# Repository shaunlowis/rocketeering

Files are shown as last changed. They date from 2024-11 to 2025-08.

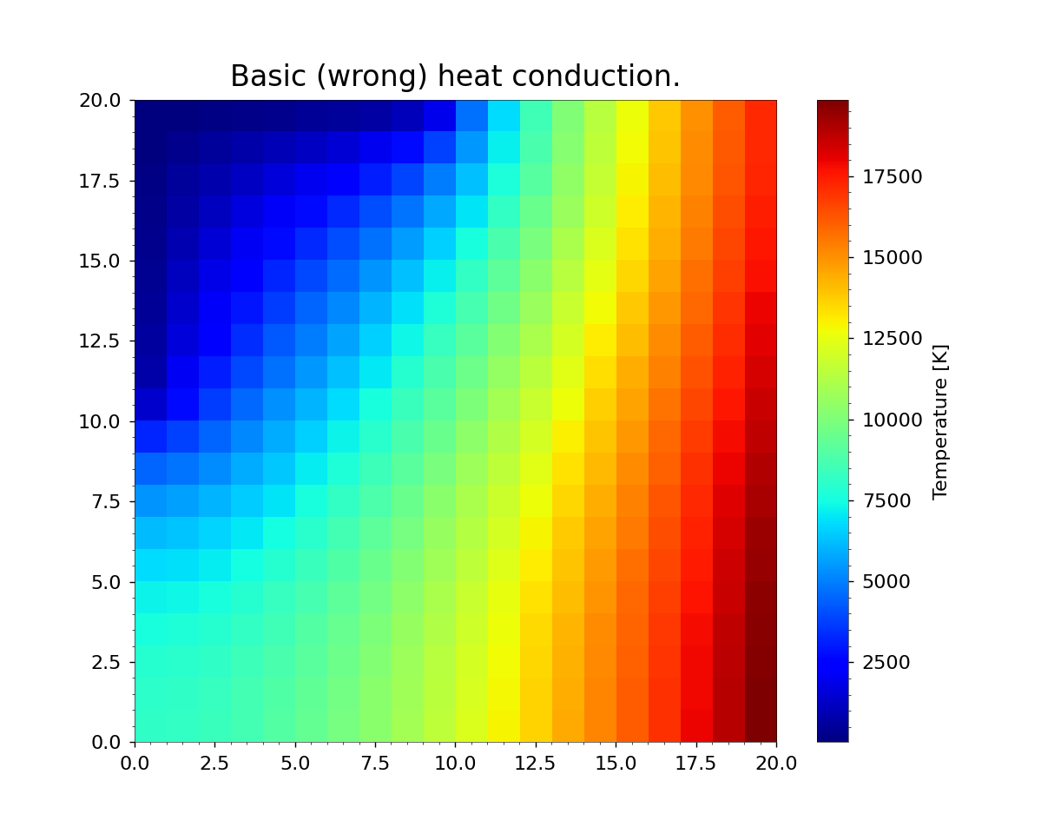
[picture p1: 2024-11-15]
modeling/thermal/babys_first_thermal.png

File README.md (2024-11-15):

# rocketeering
Documentation, progress and updates added [here](https://shaunlowis.github.io/rocketeering/)

NOTE: This guide, code, information and its authors assume no liability for outcomes or results of its use or distribution. All code and information is provided as-is for education purposes.

# Setup

Download appropriate version from [here](https://sourceforge.net/projects/sdcc/)

## Ubuntu

If on ubuntu, you should already have gcc and some form of python.

```
cd path-to-download

tar xjf sdcc-<some-version>.tar.bz

cd sdcc-<some-version>

# this will contain another file with the same name, move to that:
cd sdcc-<some-version>

# then run:
sudo ./configure

# you will probably have some missing dependencies, which I just installed with:
sudo apt install bison
sudo apt install flex
sudo apt install gputils

# repeat above until all requirements are met
# this will take quite a long time
make

# slightly faster
sudo make install

# if all went well:
sdcc -v

# which outputs something like:
SDCC : mcs51/z80/z180/r2k/r2ka/r3ka/sm83/tlcs90/ez80_z80/z80n/r800/ds390/pic16/pic14/TININative/ds400/hc08/s08/stm8/pdk13/pdk14/pdk15/mos6502/mos65c02 TD- 4.4.0 #14620 (Linux)
published under GNU General Public License (GPL)
```

Note; semi-useful guide on SDCC, see [here](https://martyn.welchs.me.uk/posts/installing-and-using-sdcc-on-linux/). For a more comprehensive guide, see the [user manual](https://sdcc.sourceforge.net/doc/sdccman.pdf).

Now we need to install the STM8 flash setup. I assume you have an ST-Link debugger, with a SWIM capable interface.
```
# wherever you want the repo to be
git clone https://github.com/vdudouyt/stm8flash.git

cd stm8flash

# dependencies:
sudo apt-get install pkg-config libusb-1.0-0-dev

make

sudo make install
```

### Download standard library
Source files for the STM8S Standard Peripheral Library are available from ST,
but it is more recommended to get the patched files from [here](https://github.com/roshbaby/stm8s-sdcc). Some further adjustments are required, depending on the
specific STM8 you have.

### Wiring the STLINK
We are using the STLINK-V2. The STM8 micro has to be debugged over SWIM.

Details for this are in section 7.3.3 [here](https://www.st.com/resource/en/user_manual/um2448-stlinkv3set-debuggerprogrammer-for-stm8-and-stm32-stmicroelectronics.pdf)

For debugging, connect SWO to the SWIM breakout header on the schematic and NRST TO NRST.

You may need to remove writing protection:

```
echo "00 00 ff 00 ff 00 ff 00 ff 00 ff" | xxd -r -p > factory_defaults.bin
stm8flash -c stlinkv2 -p stm8s007c8 -s opt -w factory_defaults.bin
```

## Flashing your first test program onto the STM8

In the `/flight_software` directory, simply do a `make flash` and if all goes well,
the compiled `main.c` file should be flashed onto your microcontroller.



Next up: make a makefile to first compile the stm8s_gpio.h and stm8s_gpio.c and 

## VS Code

Extensions:

- C/C++ for Visual Studio Code
- Hex Editor
- vscode-devdocs

## Possibly a much better setup:
https://github.com/bschwand/STM8-SPL-SDCC

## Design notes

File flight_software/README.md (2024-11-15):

# Debugger
Debug is available via [openocd](https://openocd.org/). Various windows install methods, I used [Chocolatey](https://community.chocolatey.org/packages/openocd). This installs it in `C:\ProgramData\chocolatey\lib`.

Openocd uses .cfg files to specify how to use boards (e.g. stm nucleo), targets (e.g. stm8s or even specific chips) and interfaces (e.g. stlink). These .cfg files are human readable and installed in the scripts folder of openocd, 
`C:\ProgramData\chocolatey\lib\openocd\tools\install\share\openocd\scripts`. See the [readme](https://openocd.org/doc-release/README) for more details.

`openocd -f interface/stlink-dap.cfg -f target/stm8s.cfg`

https://packages.msys2.org/package/mingw-w64-x86_64-gdb-multiarch?repo=mingw64
Needs mysys2 bin dir on path

# Coding notes/findings
## I2C is extremely tempermental. May appear to not work. Seems to randomly stop working with various history commits. Try:
 - Make clean
 - flash
 - unplug pwr, dbg, programmer
 - plug in pwr, dbg, programmer

## Printf Floats
Cannot printf floats by default, says `<NO FLOAT>`. See Compiler support routines of the [SDCC manual](docs/sdccman.pdf) for details. To enable add `-DUSE_FLOATS=1` to command line flags.
https://community.platformio.org/t/how-does-platformio-link-duse-floats-1/28458/14

## Alternate function remapping (Option byte programming)
To access the alternate pin functions you need to program the option byte accordingly. E.g. we use I2C on pins 16 & 17 which is their alternate function.

Option byte is in EEPROM and should be programmed a minimal number of times. You can use STVP as per [this guide](https://documentation.help/STM8-FlashTool-STVP/Prog0122.htm).

## Int type width only 2 bytes
On 32 bit systems ints are typically 4 bytes (STM32) and also in 64-bit AIX and Linux applications. In SDCC it is only 2 bytes (same as AVR actually) as per section 1.1 of the [SDCC manual](docs/sdccman.pdf). Therefore code such as `uint32_t comparison = 1<<(length - 1);` does not work as expected for length>16. This is because the 1 defaults to an int, and trying to leftshift it more than 16 bits is outside its width. You must specify the 1 as a 32 bit int, e.g. `uint32_t comparison = (uint32_t)1<<(length - 1);`

Lesson is to make code portable between different devices you shouldn't rely on the type widths being the same. And when taking code from forums/gpt, try specifying the compiler. Looking/Asking for C code is not enough.

## Interrupts
You need to match your interrupt handler function to the interrupt vector, so that your ISR actually gets called when the interrupt happens. This is achieved using the IRQ no assigned to the interrupt in the Interrupt Vector Mapping table of thhe STM8S007C8 Datasheet. 

E.g. UART3 RX full is number 20 with vector address 0x008058

## SD Card init/working
SD cards work based on [commands](https://chlazza.nfshost.com/sdcardinfo.html). Must send in certain order to init and expect correct responses. Demo [here](http://www.rjhcoding.com/avrc-sd-interface-3.php) but like [this guy](https://stackoverflow.com/questions/8080718/sdhc-microsd-card-and-spi-initialization) I had to also remove the CMD55 and set HCS bit in CMD1. Might be wrong.

https://github.com/joaquimorg/STM8SProjects/tree/master look in FM folder

SD card code only works when built on work laptop :)

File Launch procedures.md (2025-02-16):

# The day before
- Charge camera battery
- Charge flight comp battery
- Charge launch battery
- Clear camera SD
- Clear flight comp SD, NOT CONFIG.txt
- Pack as per below
- Charge laptops

# Packing list
- Laptops
- 5X filled 20L water containters (from work)
- 12V SLA car battery
- Rocket lower airframe
- Rocket upper airframe
- Nosecone
- Avionics bay with flight comp, flight comp battery, all fasteners
- Camera
- Camera lid
- Solid rocket motor box, containing
    - black powder
    - red plastic ejection charge cap
    - E-match
    - Motor baseplate
    - Baseplate nuts x2
    - Instructions
    - Washer for ejection charge
- Send it button with cable attached
- Flight comp debugging box with programming and debugging cables
- Spare flight comp battery
- Thermocouple
- Masking tape
- Toolbox with allen keys and screwdrivers
- Spare fasteners bag (inc spare motor washer)
- Spare ematch (red one angus)
- SD card reader
- Launch rail
- Fire extinguisher
- Water spray bottle (filled up)
- USB C charge + battery bank
- Camera lens cleaner (glasses cleaner?)

# The day of
- Ensure launch button is unplugged
- Check launch button is depressed (down = on, up = off)
- Begin recording camera
- Polisjh camera lens
- Connect battery to flight computer
- Check Green LED flashing at 20 Hz
- Check yellow LED on SD card writer is flashing
- Check RED LED not toggling
- Install AvBay
- Connect thermocouple to flight comp
- Install nosecone
- Follow motor instructions to install ejection charge
- Install motor, with backing plate
- Install E-Match as per rocket motor instructions
- Install thermocouple
- Mount to rail
- Everyone move to safe distance, from now assume rocket can launch at any point
- Connect ematch cable to battery
- Countdown
- Launch

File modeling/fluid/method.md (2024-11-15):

# OpenFOAM setup

Install from here:
https://develop.openfoam.com/Development/openfoam/-/wikis/precompiled/debian

I quickly did the basic tutorial case, but we want to use our own geometry, so let's follow:
https://www.cfd-online.com/Forums/openfoam-meshing/227156-setting-up-case-using-stl-files.html

Extended full tutorial on this is here:
https://wiki.openfoam.com/index.php?title=Tutorials

# Geometry

I whipped up the nose cone we will use for our rocket in onshape:
https://cad.onshape.com/documents/872890136eee2b11197cc0fd/w/8573091cfe1338d2f6237b9b/e/5a896293689c78557f90fb08

# Visualisation
I used ParaView. It is a little unintuitive, but you download it from here:
https://www.paraview.org/download/

Then you unzip/tar it, and you launch it with the `extracted_folder/bin/paraview` executable.

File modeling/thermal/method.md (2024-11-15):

# Heat conduction simulation to thermocouple
The thermocouple we use is intended to measure the motor's
exhaust stream. We use an RS PRO Type K, 1.5mm diameter which
has a 310 stainless steel sheath. This has a melting point of
around 1400C, which is below the expected motor temperature

## Python setup

```
# on ubuntu:
cd modeling/thermal
python3.10 -m venv .venv
source .venv/bin/activate 

python -m pip install -r requirements.txt
```

# Nose cone heating estimation
In the simplified case, estimate the expected heat of the nose
cone at different speeds. This is to inform at which mach regime
a new (metal) nose cone is required.

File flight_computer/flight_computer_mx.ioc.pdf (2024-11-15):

## flight_computer_mx Project Configuration Report

# 1. Description

## 1.1. Project

Project Name | flight_computer_mx
Board Name | No information
Generated with: | STM8CubeMX 1.5.0
Date | 06/23/2024

## 1.2. MCU

MCU Series | STM8S
MCU Line | STM8S Value Line
MCU name | STM8S007C8Tx
MCU Package | LQFP48
MCU Pin number | 48

# 2. Pinout Configuration

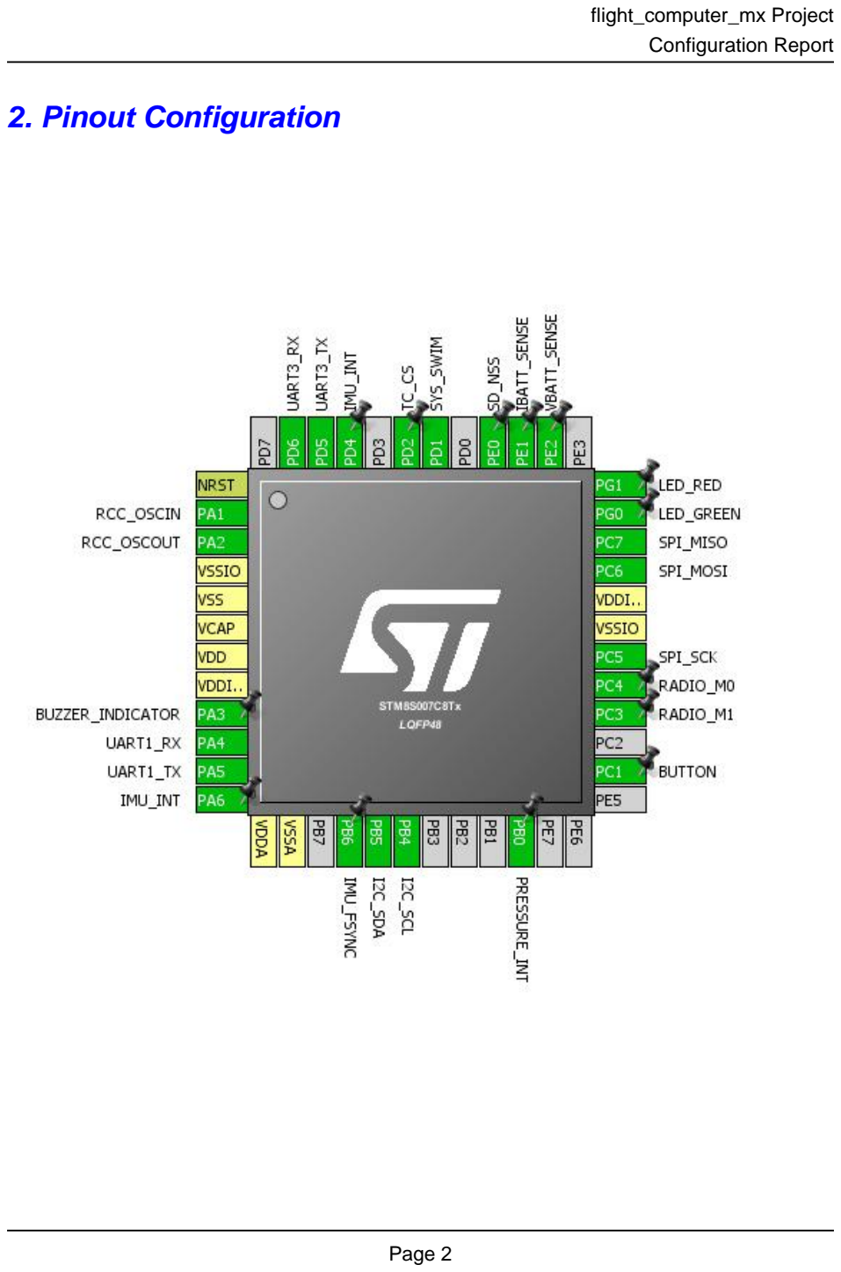
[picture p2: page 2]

# 3. Pins Configuration

Pin Number LQFP48 | Pin Name (function after reset) | Pin Type | Alternate Function(s) | Label
1 | NRST | Reset
2 | PA1 | I/O | RCC_OSCIN
3 | PA2 | I/O | RCC_OSCOUT
4 | VSSIO | Power
5 | VSS | Power
6 | VCAP | Power
7 | VDD | Power
8 | VDDIO | Power
9 | PA3 * | I/O | GPIO_Output | BUZZER_INDICATOR
10 | PA4 | I/O | UART1_RX
11 | PA5 | I/O | UART1_TX
12 | PA6 * | I/O | GPIO_Input | IMU_INT
13 | VDDA | Power
14 | VSSA | Power
16 | PB6 * | I/O | GPIO_Output | IMU_FSYNC
17 | PB5 | I/O | I2C_SDA
18 | PB4 | I/O | I2C_SCL
22 | PB0 * | I/O | GPIO_Input | PRESSURE_INT
26 | PC1 * | I/O | GPIO_Input | BUTTON
28 | PC3 * | I/O | GPIO_Output | RADIO_M1
29 | PC4 * | I/O | GPIO_Output | RADIO_M0
30 | PC5 | I/O | SPI_SCK
31 | VSSIO | Power
32 | VDDIO | Power
33 | PC6 | I/O | SPI_MOSI
34 | PC7 | I/O | SPI_MISO
35 | PG0 * | I/O | GPIO_Output | LED_GREEN
36 | PG1 * | I/O | GPIO_Output | LED_RED
38 | PE2 * | I/O | GPIO_Analog | VBATT_SENSE
39 | PE1 * | I/O | GPIO_Analog | IBATT_SENSE
40 | PE0 * | I/O | GPIO_Output | SD_NSS
42 | PD1 | I/O | SYS_SWIM
43 | PD2 * | I/O | GPIO_Output | TC_CS
45 | PD4 * | I/O | GPIO_Input | IMU_INT
46 | PD5 | I/O | UART3_TX
47 | PD6 | I/O | UART3_RX

## * The pin is affected with an I/O function

# 4. Clock Tree Configuration

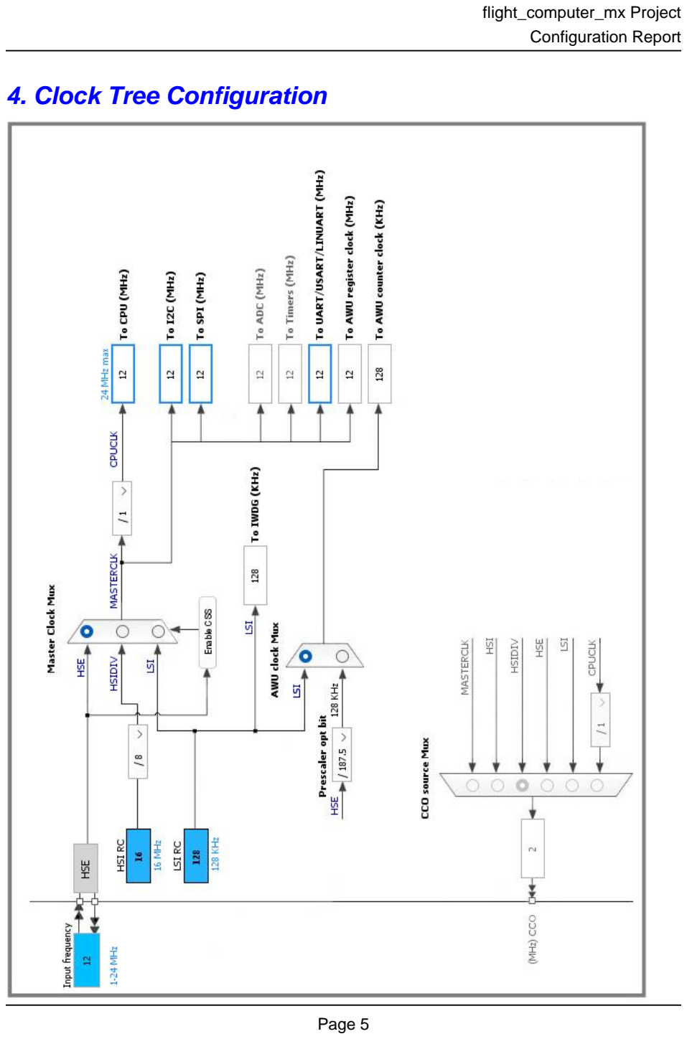
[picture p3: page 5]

# 5. Power Consumption Calculator report

## 5.1. Microcontroller Selection

Series | STM8S
Line | STM8S Value Line
MCU | STM8S007C8Tx
Datasheet | 22171_Rev5

## 5.2. Parameter Selection

Temperature | 25
Vdd | null

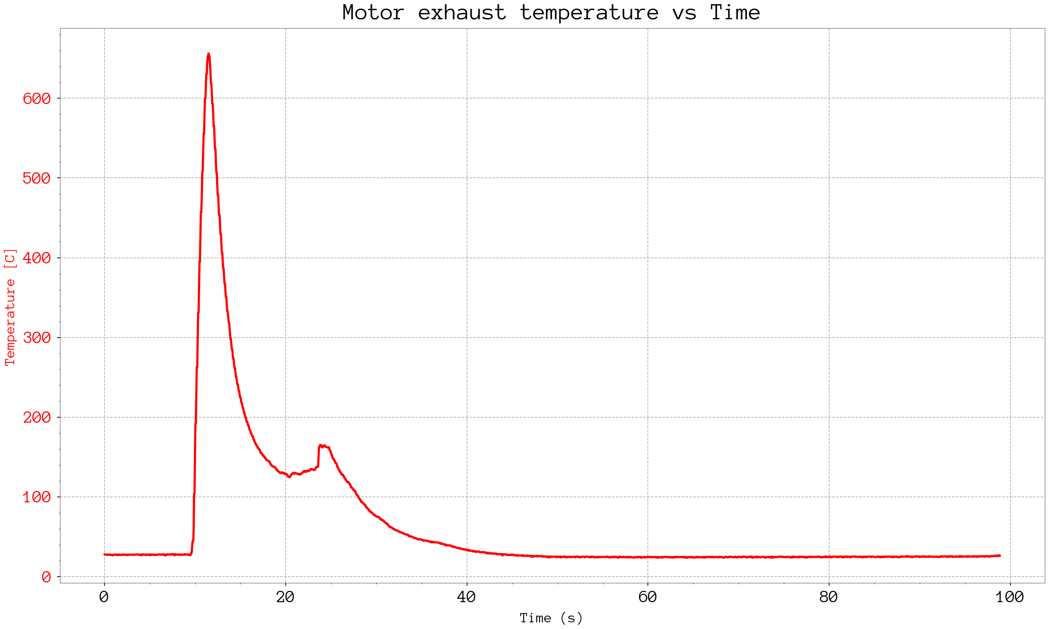
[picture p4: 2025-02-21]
thermocouple.png

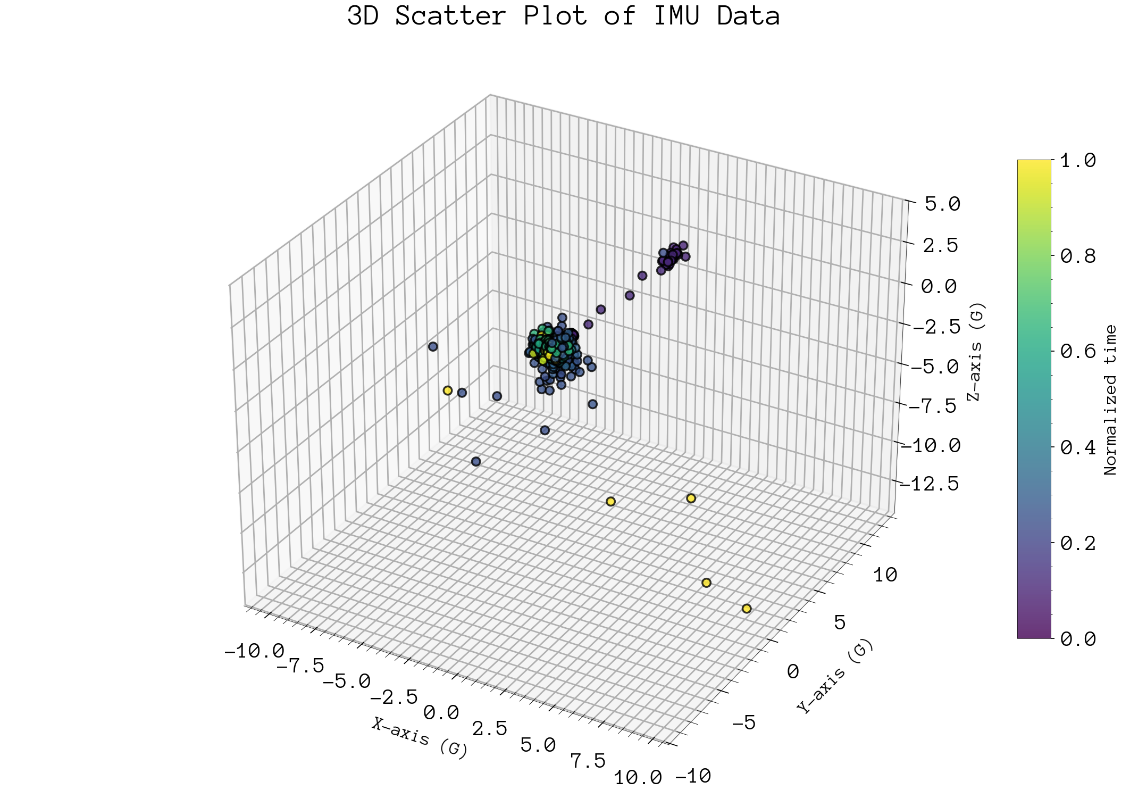
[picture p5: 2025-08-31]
imu_data.png

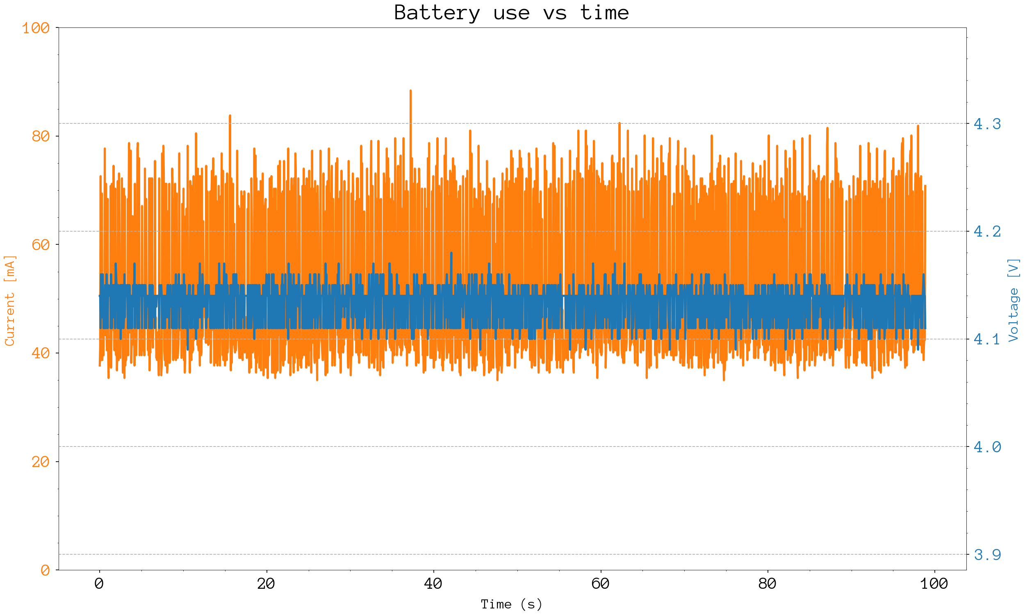
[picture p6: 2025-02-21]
battery.png

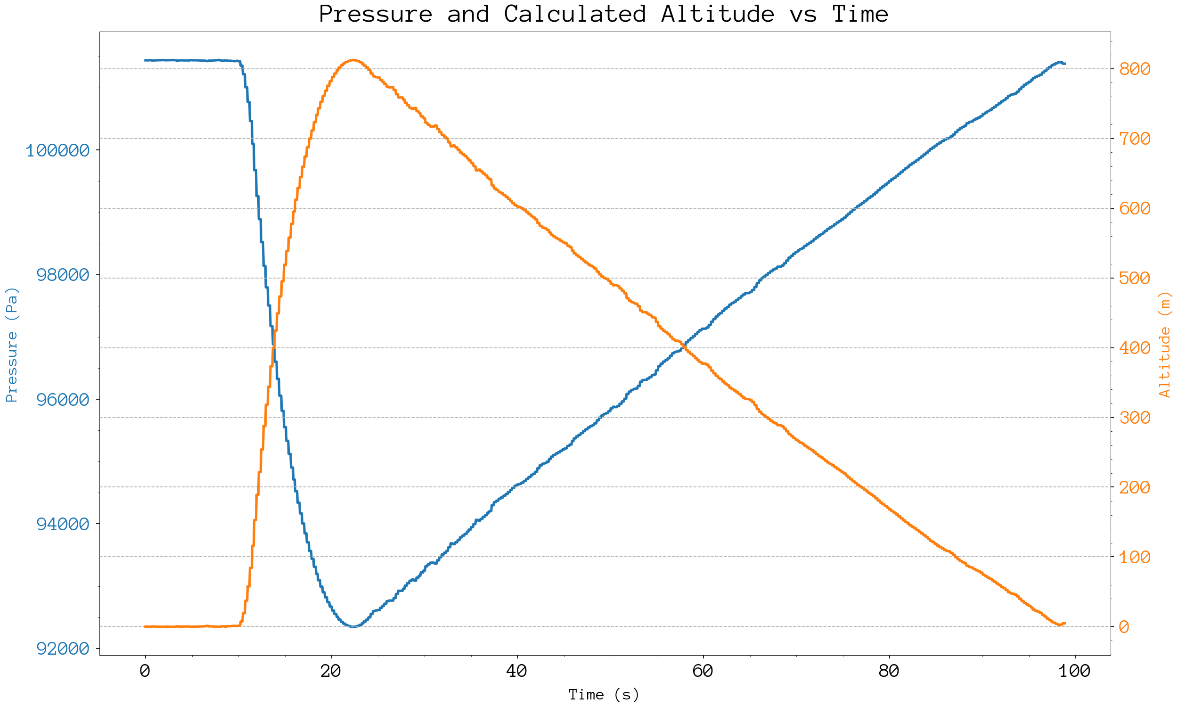
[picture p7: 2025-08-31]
altitude.png

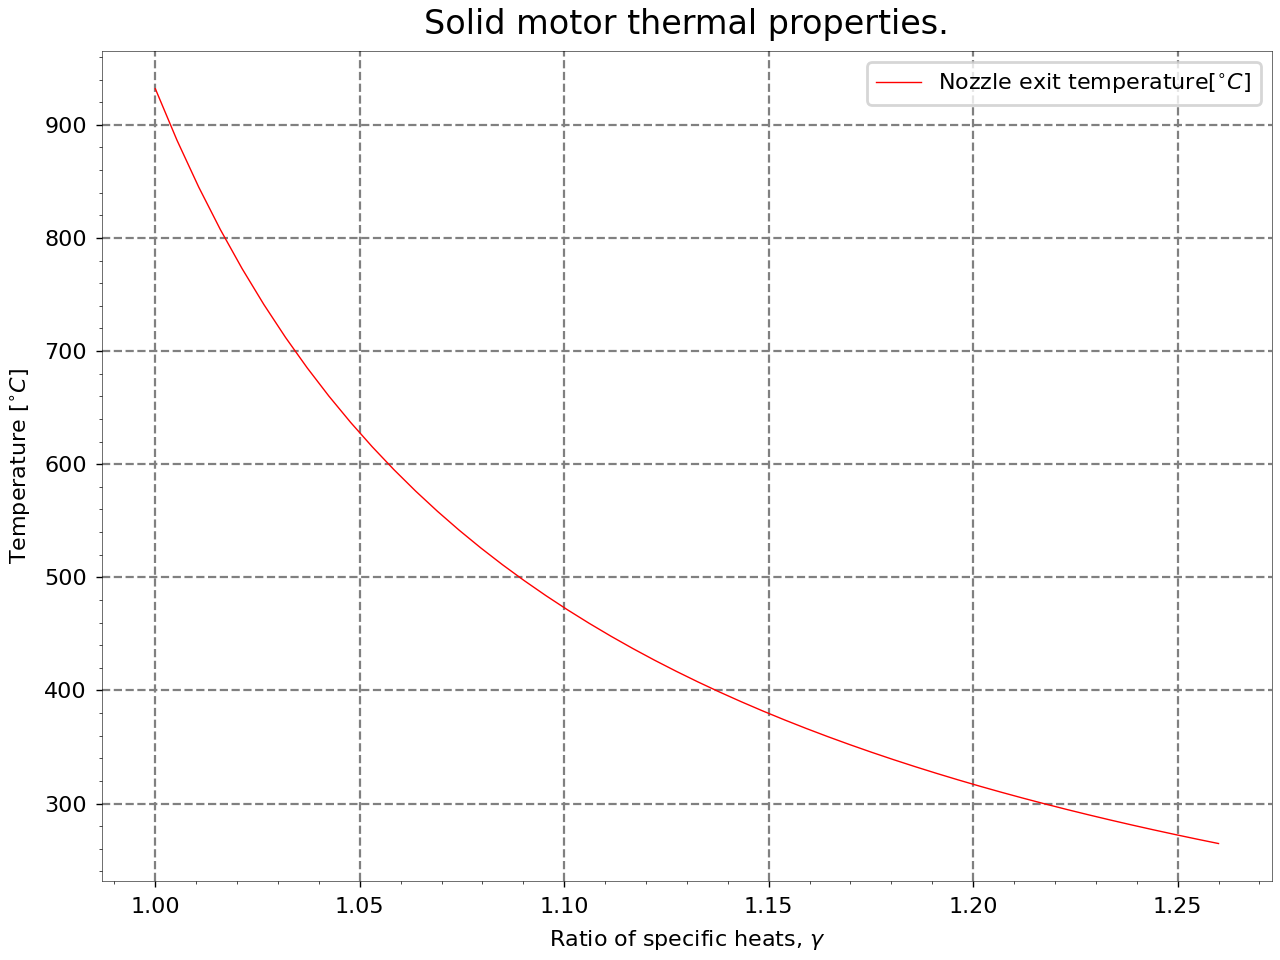
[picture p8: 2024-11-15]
modeling/thermal/nozzle_exit_temp.png

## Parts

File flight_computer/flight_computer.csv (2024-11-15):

Source: | C:\Users\angus\Documents\Electronics\Projects\rocketeering\flight_computer\flight_computer.kicad_sch
Date: | 30/05/2024 8:59:11 PM
Tool: | Eeschema 7.0.6
Generator: | C:\Program Files\KiCad\7.0\bin\scripting\plugins/bom_csv_grouped_by_value.py
Component Count: | 94
Collated Components:
Item | Qty | Reference(s) | Value | LibPart | Footprint | Datasheet | DNP | ESR | MPN | Manufacturer PN | Max Current | Power | Supplier | Supplier PN | Voltage
1 | 1 | BZ1 | Buzzer_indicator | Device:Buzzer | my_footprints:buzzer_Dia9.2mm_P5mm | https://www.digikey.co.nz/en/products/detail/soberton-inc/WST-0906T/16354832 |  |  |  | WST-0906T |  |  | Digikey | 433-WST-0906T-ND
2 | 8 | C1, C3, C10, C11, C17, C19, C20, C22 | 10uF | Device:C | Capacitor_SMD:C_0402_1005Metric | https://wmsc.lcsc.com/wmsc/upload/file/pdf/v2/lcsc/2304140030_Samsung-Electro-Mechanics-CL10A106KP8NNNC_C19702.pdf |  |  |  | CL10A106KP8NNNC |  |  | JLC | C19702 | 10V
3 | 16 | C2, C4, C8, C9, C12, C16, C18, C24, C25, C30, C33, C35, C36, C37, C38, C39 | 100nF | Device:C | Capacitor_SMD:C_0402_1005Metric | https://wmsc.lcsc.com/wmsc/upload/file/pdf/v2/lcsc/2304140030_Samsung-Electro-Mechanics-CL05B104KO5NNNC_C1525.pdf |  |  |  | CL05B104KO5NNNC |  |  | JLC | C1525 | 16V
4 | 2 | C5, C6 | 33pF | Device:C | Capacitor_SMD:C_0402_1005Metric | https://wmsc.lcsc.com/wmsc/upload/file/pdf/v2/lcsc/2304140030_FH--Guangdong-Fenghua-Advanced-Tech-0402CG330J500NT_C1562.pdf |  |  |  | 0402CG330J500NT |  |  | C1562 | JLC | 50V
5 | 4 | C7, C21, C23, C34 | 1uF | Device:C | Capacitor_SMD:C_0402_1005Metric | https://wmsc.lcsc.com/wmsc/upload/file/pdf/v2/lcsc/2304140030_Samsung-Electro-Mechanics-CL05A105KA5NQNC_C52923.pdf |  |  |  | CL05A105KA5NQNC |  |  | JLC | C52923 | 25V
6 | 2 | C13, C14 | 1.8nF | Device:C | Capacitor_SMD:C_0402_1005Metric | https://connect.kemet.com:7667/gateway/IntelliData-ComponentDocumentation/1.0/download/datasheet/C0402C182K3RACTU |  |  |  | 399-17371-1-ND |  |  | Digikey | C0402C182K3RAC7867
7 | 1 | C15 | 22pF | Device:C | Capacitor_SMD:C_0402_1005Metric | https://www.digikey.co.nz/en/products/detail/kemet/C0402C220K4RAC7867/8572389 |  |  |  | 399-17554-1-ND |  |  | Digikey | C0402C220K4RAC7867
8 | 2 | C26, C31 | 2.2uF | Device:C | Capacitor_SMD:C_0402_1005Metric | https://wmsc.lcsc.com/wmsc/upload/file/pdf/v2/lcsc/2304140030_Samsung-Electro-Mechanics-CL05A225MQ5NSNC_C12530.pdf |  |  |  | CL05A225MQ5NSNC |  |  | JLC | C12530 | 6.3V
9 | 2 | C27, C32 | 10nF | Device:C | Capacitor_SMD:C_0402_1005Metric | https://wmsc.lcsc.com/wmsc/upload/file/pdf/v2/lcsc/2304140030_Samsung-Electro-Mechanics-CL05B103KB5NNNC_C15195.pdf |  |  |  | CL05B103KB5NNNC |  |  | JLC | C15195 | 50V
10 | 2 | C28, C29 | 100pF | Device:C | Capacitor_SMD:C_0402_1005Metric | https://wmsc.lcsc.com/wmsc/upload/file/pdf/v2/lcsc/2304140030_FH--Guangdong-Fenghua-Advanced-Tech-0402CG101J500NT_C1546.pdf |  |  |  | 0402CG101J500NT |  |  | JLC | C1546 | 50V
11 | 1 | D1 | Green | Device:LED | LED_SMD:LED_0805_2012Metric | https://wmsc.lcsc.com/wmsc/upload/file/pdf/v2/lcsc/1806151820_Hubei-KENTO-Elec-KT-0805G_C2297.pdf |  |  |  | KT-0805G |  |  | JLC | C2297
12 | 1 | D2 | Red | Device:LED | LED_SMD:LED_0805_2012Metric | https://wmsc.lcsc.com/wmsc/upload/file/pdf/v2/lcsc/2304140030_Foshan-NationStar-Optoelectronics-NCD0805R1_C84256.pdf |  |  |  | NCD0805R1 |  |  | JLC | C84256
13 | 1 | D3 | 5.1V | Device:D_Zener | Package_TO_SOT_SMD:SOT-23 | https://www.mccsemi.com/pdf/Products/BZX84C(B)2V4~BZX84C(B)75(SOT-23).pdf |  |  |  | BZX84C5V1-TP |  |  | Digikey | BZX84C5V1-TPMSDKR-ND
14 | 1 | D4 | Blue | Device:LED | LED_SMD:LED_0603_1608Metric | https://wmsc.lcsc.com/wmsc/upload/file/pdf/v2/lcsc/2205171716_Everlight-Elec-19-217-BHC-ZL1M2RY-6T_C2986058.pdf |  |  |  | 19-217/BHC-ZL1M2RY/6T |  |  | JLC | C2986058
15 | 1 | F1 | 250mA | Device:Fuse | Fuse:Fuse_0603_1608Metric | http://www.kamaya.co.jp/upload/products_pdf/kamaya_products(FMC)_english_20170203_122640.pdf |  |  |  | FMC16501WBTP |  |  | Digikey | 2315-FMC16501WBTPDKR-ND
16 | 1 | J1 | Conn_02x05_Odd_Even | Connector_Generic:Conn_02x05_Odd_Even | Connector_PinHeader_2.54mm:PinHeader_2x05_P2.54mm_Vertical | ~ |  |  |  | 302-S101 |  |  | Digikey | ED1543-ND
17 | 1 | J2 | MEM2061-01-188-00-A_REVA | my_library:MEM2061-01-188-00-A_REVA | my_footprints:MEM2061-01-188-00-A | https://gct.co/files/specs/mem2061-spec.pdf |  |  |  | MEM2061-01-188-00-A |  |  | Digikey | 2073-MEM2061-01-188-00-ACT-ND
18 | 1 | J3 | Conn_01x02 | Connector_Generic:Conn_01x02 | Connector_JST:JST_PH_S2B-PH-K_1x02_P2.00mm_Horizontal | https://www.jst-mfg.com/product/pdf/eng/ePH.pdf |  |  |  | S2B-PH-K-S |  |  | Digikey | 455-1719-ND
19 | 1 | J7 | Conn_01x07_MountingPin | Connector_Generic_MountingPin:Conn_01x07_MountingPin | my_footprints:E220-400T30D | ~ |  |  |  | E220-400T30D
20 | 1 | L1 | 1.5uH | Device:L | Inductor_SMD:L_1008_2520Metric | https://search.murata.co.jp/Ceramy/image/img/P02/JELF243B-0019.pdf |  | 88mOhm |  | LQM2HPN1R5MG0L | 1.5A |  | Digikey | 490-5113-1-ND
21 | 1 | L2 | 3.3uH | Device:L | Inductor_SMD:L_0805_2012Metric | https://product.tdk.com/en/system/files |  |  |  | MLZ2012N3R3LT000 | 750mA |  | Digikey | 445-6759-1-ND
22 | 1 | Q1 | Q_NPN_BEC | Device:Q_NPN_BEC | Package_TO_SOT_SMD:SOT-23-3 | https://www.onsemi.com/download/data-sheet/pdf/bc846alt1-d.pdf |  |  |  | BC847CLT3G |  |  | Digikey | BC847CLT3GOSCT-ND
23 | 1 | Q2 | Q_NMOS_GSD | Device:Q_NMOS_GSD | Package_TO_SOT_SMD:SOT-323_SC-70 | https://www.panjit.com.tw/upload/datasheet/PJC7404.pdf |  |  |  | PJC7404_R1_00001 |  |  | Digikey | 3757-PJC7404_R1_00001CT-ND
24 | 5 | R1, R18, R22, R24, R25 | 150R | Device:R | Resistor_SMD:R_0402_1005Metric | https://wmsc.lcsc.com/wmsc/upload/file/pdf/v2/lcsc/2205311900_UNI-ROYAL-Uniroyal-Elec-0402WGF1500TCE_C25082.pdf |  |  |  | 0402WGF1500TCE |  |  | JLC | C25082
25 | 1 | R2 | 470R | Device:R | Resistor_SMD:R_0402_1005Metric | https://wmsc.lcsc.com/wmsc/upload/file/pdf/v2/lcsc/2205311900_UNI-ROYAL-Uniroyal-Elec-0402WGF4700TCE_C25117.pdf |  |  |  | 0402WGF4700TCE |  |  | JLC | C25117
26 | 7 | R3, R6, R14, R15, R16, R21, R23 | 1M | Device:R | Resistor_SMD:R_0402_1005Metric | https://wmsc.lcsc.com/wmsc/upload/file/pdf/v2/lcsc/2206010030_UNI-ROYAL-Uniroyal-Elec-0402WGF1004TCE_C26083.pdf |  |  |  | 0402WGF1004TCE |  |  | JLC | C26083
27 | 2 | R4, R5 | 4.7k | Device:R | Resistor_SMD:R_0402_1005Metric | https://wmsc.lcsc.com/wmsc/upload/file/pdf/v2/lcsc/2206010045_UNI-ROYAL-Uniroyal-Elec-0402WGF4701TCE_C25900.pdf |  |  |  | 0402WGF4701TCE |  |  | JLC | C25900
28 | 3 | R7, R10, R11 | 1k | Device:R | Resistor_SMD:R_0402_1005Metric | https://wmsc.lcsc.com/wmsc/upload/file/pdf/v2/lcsc/2206010216_UNI-ROYAL-Uniroyal-Elec-0402WGF1001TCE_C11702.pdf |  |  |  | 0402WGF1001TCE |  |  | JLC | C11702
29 | 3 | R8, R19, R20 | 0R | Device:R | Resistor_SMD:R_0402_1005Metric | https://wmsc.lcsc.com/wmsc/upload/file/pdf/v2/lcsc/2206010216_UNI-ROYAL-Uniroyal-Elec-0402WGF0000TCE_C17168.pdf |  |  |  | 0402WGF0000TCE |  |  | JLC | C17168
30 | 1 | R9 | 0.1R | Device:R | Resistor_SMD:R_1206_3216Metric | https://wmsc.lcsc.com/wmsc/upload/file/pdf/v2/lcsc/2205311900_UNI-ROYAL-Uniroyal-Elec-1206W4F100LT5E_C25334.pdf |  |  |  | 1206W4F100LT5E |  | 250mW | JLC | C25334
31 | 6 | R12, R26, R27, R28, R29, R30 | 10k | Device:R | Resistor_SMD:R_0402_1005Metric | https://wmsc.lcsc.com/wmsc/upload/file/pdf/v2/lcsc/2206010100_UNI-ROYAL-Uniroyal-Elec-0402WGF1002TCE_C25744.pdf |  |  |  | 0402WGF1002TCE |  |  | JLC | C25744
32 | 1 | R13 | 68k | Device:R | Resistor_SMD:R_0402_1005Metric | https://wmsc.lcsc.com/wmsc/upload/file/pdf/v2/lcsc/2206010030_UNI-ROYAL-Uniroyal-Elec-0402WGF6802TCE_C36871.pdf |  |  |  | 0402WGF6802TCE |  |  | JLC | C36871
33 | 2 | SW1, SW2 | SW_Push | Switch:SW_Push | my_footprints:KMR2_1 | https://www.ckswitches.com/media/1479/kmr2.pdf |  |  |  | KMR231GLFS |  |  | Digikey | 401-1429-1-ND
34 | 1 | U1 | STM8S007C8T6TR | my_library:STM8S007C8T6 | Package_QFP:LQFP-48_7x7mm_P0.5mm | https://www.st.com/content/ccc/resource/technical/document/datasheet/03/af/ba/15/7c/fe/4c/91/DM00037365.pdf/files/DM00037365.pdf/jcr:content/translations/en.D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 |  |  |  | STM8S007C8T6TR |  |  | Digikey | 497-18848-1-ND
35 | 1 | U2 | NCS325 | Amplifier_Operational:NCS325 | Package_TO_SOT_SMD:SOT-23-5 | http://www.onsemi.com/pub/Collateral/NCS325-D.PDF |  |  |  | NCS325SN2T1G |  |  | Digikey | NCS325SN2T1GOSCT-ND
36 | 1 | U3 | TPS63051RMWR | my_library:TPS63051RMWR | my_footprints:VQFN-12-HR_2.5x2.5mm_P0.5mm | https://www.ti.com/lit/ds/symlink/tps63051.pdf?ts=1714117211770 |  |  | TPS63051RMWR | TPS63051RMWR |  |  | Digikey | 296-42650-1-ND
37 | 1 | U4 | MIC94310-GYMT-TR | my_library:MIC94310-GYMT-TR | my_footprints:TDFN-4-1EP_1.2x1.6mm_P0.5mm | http://ww1.microchip.com/downloads/en/devicedoc/mic94310.pdf |  |  |  | MIC94310-GYMT-TR |  |  | Digikey | 576-4012-1-ND
38 | 1 | U5 | SPL07-003 | my_library:SPL07-003 | Package_LGA:ST_HLGA-10_2x2mm_P0.5mm_LayoutBorder3x2y | https://mm.digikey.com/Volume0/opasdata/d220001/medias/docus/4843/SPL07-003.pdf |  |  |  | SPL07-003 |  |  | Digikey | 4719-SPL07-003CT-ND
39 | 1 | U6 | YIC31612EBGG | my_library:YIC31612EBGG | my_footprints:24-SMD Module | https://www.yic.com.tw/wp-content/uploads/2022/01/YIC31612EBGG.pdf |  |  |  | YIC31612EBGG |  |  | Digikey | 3155-YIC31612EBGGCT-ND
40 | 1 | U7 | ICM-42670-P | my_library:ICM-42670-P | Package_LGA:LGA-14_3x2.5mm_P0.5mm_LayoutBorder3x4y | https://product.tdk.com/system/files/dam/doc/product/sensor/mortion-inertial/imu/data_sheet/ds-000451-icm-42670-p.pdf |  |  |  | ICM-42670-P |  |  | Digikey | 1428-ICM-42670-PCT-ND
41 | 1 | U8 | MAX31855KASA | Sensor_Temperature:MAX31855KASA | Package_SO:SOIC-8_3.9x4.9mm_P1.27mm | http://datasheets.maximintegrated.com/en/ds/MAX31855.pdf |  |  |  | MAX31855KASA+T |  |  | Digikey | MAX31855KASA+TCT-ND
42 | 1 | U9 | Antenna_GPS | my_library:1582AT54A0045 | my_footprints:1582AT54A0045 | https://www.johansontechnology.com/datasheets/1582AT54A0045/1582AT54A0045.pdf |  |  |  | 1582AT54A0045 |  |  | Digikey | 712-1582AT54A0045001ECT-ND
43 | 1 | Y1 | 12MHz | Device:Crystal_GND24 | Crystal:Crystal_SMD_3225-4Pin_3.2x2.5mm | https://wmsc.lcsc.com/wmsc/upload/file/pdf/v2/lcsc/2403291504_YXC-X322512MSB4SI_C9002.pdf |  |  |  | X322512MSB4SI |  |  | JLC | C9002

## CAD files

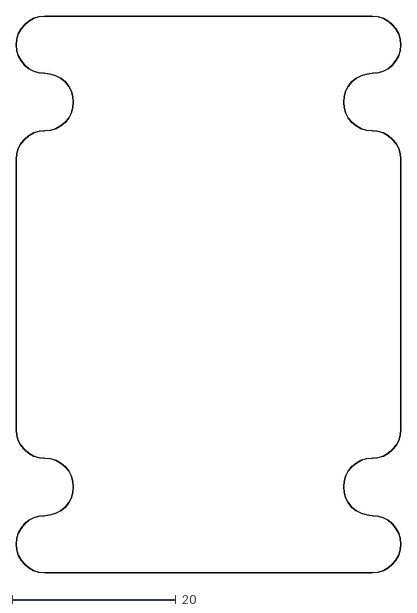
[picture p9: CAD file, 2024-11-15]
flight_computer/Flight computer outline.dxf
47.0 x 68.0

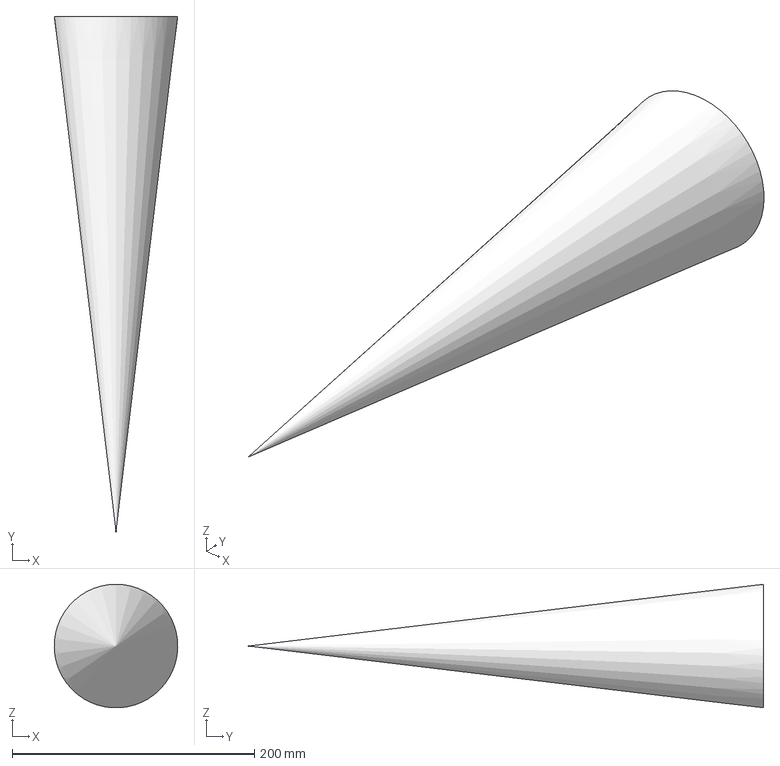
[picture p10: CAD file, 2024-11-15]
modeling/fluid/meshing/Nose cone.step
102.0 x 425.0 x 101.9 mm

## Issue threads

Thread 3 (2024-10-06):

Battery V/I sensing to wrong pins

AngusEason, 2024-10-06:
Not routed to analog pins

shaunlowis, 2024-10-11:
Fixed with rework wire

Closed 2024-10-11.

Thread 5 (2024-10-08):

Button footprints are wrong

AngusEason, 2024-10-08:

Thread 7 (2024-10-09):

Complete thermocouple setup

shaunlowis, 2024-10-09:
With current micro

shaunlowis, 2024-10-12:
got SPI init and raw reads done, need to do conversion and validation.

shaunlowis, 2024-11-01:
Adding datasheet to here for convenience:
https://www.analog.com/media/en/technical-documentation/data-sheets/max31855.pdf

shaunlowis, 2024-11-10:
Closed with latest FC_dev merge

Closed 2024-11-10.

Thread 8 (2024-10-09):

Visualise collected data

shaunlowis, 2024-10-09:
Doing a Rust backend and javascript frontend could be quite cool, here's what ChatGPT had to say:

Integrating Rust with a web interface for live plotting is a great way to make your data visualization accessible and interactive. You can achieve this by using Rust for the backend, serving the live data, and a JavaScript library like **Plotly.js** or **Chart.js** for rendering the live plots in a web browser.

Here’s a guide on how to do this with Rust using the **Rocket** web framework (for the backend) and **Plotly.js** (for the frontend).

### 1. **Setup Rocket Web Framework**

First, you'll need to install **Rocket**, a fast and flexible web framework for Rust.

#### In `Cargo.toml`:
Add the dependencies for `Rocket` and `Serde` (for serialization) in your `Cargo.toml`:

```toml
[dependencies]
rocket = { version = "0.5.0-rc.2", features = ["json"] }
serde = { version = "1.0", features = ["derive"] }
serde_json = "1.0"
tokio = { version = "1", features = ["full"] }
```

### 2. **Backend: Serving Live Data**

We’ll create a simple REST API endpoint that streams live data to the frontend. In a real-world scenario, this data would come from the radio link, but we’ll simulate it here.

#### `src/main.rs`:

```rust
#[macro_use] extern crate rocket;

use rocket::serde::{Serialize, json::Json};
use std::{thread, time::Duration};

// Simulated data point
#[derive(Serialize)]
struct DataPoint {
    x: u32,
    y: u32,
}

// API route that simulates live data
#[get("/live_data")]
fn live_data() -> Json<DataPoint> {
    // Simulate generating data
    let mut x = 0;
    let y = (x * x) % 100;
    x += 1;
    thread::sleep(Duration::from_millis(100));  // Simulate data delay
    Json(DataPoint { x, y })
}

#[launch]
fn rocket() -> _ {
    rocket::build().mount("/", routes![live_data])
}
```

This backend will serve live data in JSON format whenever the client (frontend) requests it.

### 3. **Frontend: Plotting with Plotly.js**

Now, create a simple HTML file that will request the data from the backend and plot it using **Plotly.js**.

#### `static/index.html`:

```html
<!DOCTYPE html>
<html lang="en">
<head>
    <meta charset="UTF-8">
    <meta name="viewport" content="width=device-width, initial-scale=1.0">
    <title>Live Plot</title>
    <script src="https://cdn.plot.ly/plotly-latest.min.js"></script>
</head>
<body>
    <h1>Live Data Plot</h1>

    <script>
        const trace1 = {
            x: [],
            y: [],
            mode: 'lines+markers',
            type: 'scatter'
        };

        const data = [trace1];
        Plotly.newPlot('plot', data);

        // Function to fetch live data and update plot
        async function fetchDataAndPlot() {
            try {
                const response = await fetch("/live_data");
                const dataPoint = await response.json();
                trace1.x.push(dataPoint.x);
                trace1.y.push(dataPoint.y);
                Plotly.update('plot', { x: [trace1.x], y: [trace1.y] });
            } catch (error) {
                console.error("Error fetching data:", error);
            }
        }

        // Fetch data every 1 second
        setInterval(fetchDataAndPlot, 1000);
    </script>
</body>
</html>
```

### Explanation:
1. **HTML Structure**:
   - We import the **Plotly.js** library, which allows us to create and update interactive plots in the browser.
   - A `<div>` with the id `plot` is where the plot will be rendered.

2. **JavaScript Code**:
   - We create an empty **trace** object with `x` and `y` arrays and define it as a line plot.
   - The `fetchDataAndPlot()` function fetches data from the `/live_data` endpoint and pushes the new data points to the `x` and `y` arrays. It then calls `Plotly.update()` to refresh the plot with the new data.
   - We use `setInterval()` to fetch new data every second and update the plot continuously.

### 4. **Serving Static Files with Rocket**

Rocket can serve static files, so let’s modify the Rust backend to serve our `index.html` file.

#### `src/main.rs` (Extended):

```rust
#[macro_use] extern crate rocket;

use rocket::serde::{Serialize, json::Json};
use std::{thread, time::Duration};
use rocket::fs::FileServer;

// Simulated data point
#[derive(Serialize)]
struct DataPoint {
    x: u32,
    y: u32,
}

// API route that simulates live data
#[get("/live_data")]
fn live_data() -> Json<DataPoint> {
    let mut x = 0;
    let y = (x * x) % 100;
    x += 1;
    thread::sleep(Duration::from_millis(100));
    Json(DataPoint { x, y })
}

#[launch]
fn rocket() -> _ {
    rocket::build()
        .mount("/", routes![live_data])
        .mount("/", FileServer::from("static"))  // Serve static files from the "static" directory
}
```

Now, Rocket will serve your `index.html` file from the `static/` directory when you open `localhost:8000` in a browser, and the `/live_data` API will serve live data to update the plot.

### 5. **Running the Application**

1. Create the `static` directory in your project folder and put `index.html` inside it.
2. Build and run the Rocket app:

```bash
cargo run
```

3. Open a browser and navigate to `http://localhost:8000/`. You should see the plot updating with live data every second.

### 6. **Summary**

- **Rust** (backend): Serves the live data through a REST API using Rocket.
- **Plotly.js** (frontend): Fetches the data from the API and plots it in real-time.

You can modify the Rust code to get real data from your radio link or serial device and send it to the frontend, while Plotly.js will keep updating the graph.

Let me know if you'd like to dive deeper into any part or add more features!

shaunlowis, 2024-11-01:
For Dry run, only plots of collected data is needed, not live data, so a simple python script is sufficient.

shaunlowis, 2024-11-26:
Will reopen for later if needed

Closed 2024-11-26.

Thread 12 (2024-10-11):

Purchase missing components

AngusEason, 2024-10-11:
- Battery
- Battery connector
-

AngusEason, 2024-10-12:
Purchased 13/10/24 from ali express and midkits nz

Closed 2024-10-12.

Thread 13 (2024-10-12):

Perform mods to airframe

AngusEason, 2024-10-12:
- Load calcs for avbay mounting
- Drill holes for mounting avbay
- Print updated avbay and install M4 heat set inserts
- Test fit mounting avbay
- Install thermocouple wire and connectors down to the engine (dilling as required).
- Secure wires with epoxy

shaunlowis, 2024-11-26:
- Test thermocouple connector mount, see [here](https://cad.onshape.com/documents/872890136eee2b11197cc0fd/w/8573091cfe1338d2f6237b9b/e/51cf60da6aae13c0dbae036a)
- Made new drill jig, fit to air frame and test, see [here](https://cad.onshape.com/documents/872890136eee2b11197cc0fd/w/8573091cfe1338d2f6237b9b/e/d5691ce231b18a61533ffa2f)

shaunlowis, 2024-12-18:
- Holes drilled by big A
- Dremelled a window for the camera, looks good
- Thermocouple TODO

shaunlowis, 2025-01-22:
Donezo, all mounted.

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

Closed 2025-01-22.

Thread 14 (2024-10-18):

Flight computer freezes after some time and never recovers

AngusEason, 2024-10-18:
Either need to solve root issue or implement watchdog.

Adding watchdog is probably good as a backup, good to find rot cause though.

AngusEason, 2024-10-23:
Fixed by making GPS circular buffer read atomic

AngusEason, 2024-11-06:
Seems to be back. Circ buff read is atomic and still occurs.

AngusEason, 2024-11-13:
Adding random delay does help, but doesnt make it fully go away. Watchdog works but not 100% reliable, sometimes the reboot gets stuck in gps_init when trying to disable/enable interrupts

shaunlowis, 2024-11-26:
@AngusEason this seems okayish for the dry run, change milestone to next launch?

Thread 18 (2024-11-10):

Thermal analysis

shaunlowis, 2024-11-10:
- Check for what speed we need a new nosecone
- Casing for thermocouple for measuring motor exhaust temps.

Made branch /feature/heat_modeling

shaunlowis, 2024-11-10:
Made progress on this, have an estimate on T exhaust for range of gamma values. This will let us guess the chemical composition of the OTC motor if we feel like doing more modeling later.

The conductive heat transfer model, using a diffusion model, is very wrong, but some experimenting with boundary and initial conditions seems promising. This could inform the thermocouple casing design.

Closed 2025-02-21.

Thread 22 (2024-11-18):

Mech stuff

shaunlowis, 2024-11-18:
Set of physical modifications needed to airframe, or additional parts needed before the first dry run of launch.

1. Install av bay (camera + flight comp) into nose cone connector section:
- CAD up components, line up drill sections through air frame and make new jig, ideal is to be flat/near inner cardboard coupler.

2. Drill hole for camera once av bay is installed, check if perspex sheet is needed.
3. Mount in motor chamber area for thermocouple. CAD up the components here and make a holding jig
4. Wire through thermocouple leads from avbay through to motor chamber.

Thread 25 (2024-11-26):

E fuse

shaunlowis, 2024-11-26:
Get a big red button and wire up to E fuse (First Fire igniter), from [this listing](https://www.apogeerockets.com/Rocket_Motors/AeroTech_Accessories/First_Fire_Starter) the supplied e-match requires a 12V input to work. From [this forum post](https://www.rocketryforum.com/threads/opinions-wanted-aerotech-firstfire-ignitors.180993/), no other mods are needed.

shaunlowis, 2025-01-22:
Made box, tested it.

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

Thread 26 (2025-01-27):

Launch location admin

shaunlowis, 2025-01-27:
- Email farmer for permission.
- get a NOTAM.
- Run Openrocket sim and check that apogee < 2500ft, if not, re-run with higher mass.
- finish organising/fabricating launch rail.
- test igniter box button wiring.

Closed 2025-02-16.

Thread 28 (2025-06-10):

Find stm32 drop-in replacement

shaunlowis, 2025-06-10:
Current model used is the STM8S003F3, with pin layout LQFP32 7x7 mm. Datasheet here:
https://www.st.com/resource/en/datasheet/stm8s003f3.pdf

There's actually a bunch of stm32's that have the same layout for LQFP32 7x7:
https://www.st.com/en/microcontrollers-microprocessors/stm32g4-series/products.html

Keeping in mind that we want to do a PCB rework anyways to fix:
- Button not working.
- Debug pins not working.
- SD card not working.
- Either getting the board assembled or make the assembly easier.

Pin layout matching exactly doesn't matter, but it would be cool to keep the form factor of the board.
Also, this time getting a dev board would make life a lot easier, rather than debugging software and hardware at the same time.

Also also, check whether the selected board has an easy debug setup, that was ~a fuckup~ difficult last time.

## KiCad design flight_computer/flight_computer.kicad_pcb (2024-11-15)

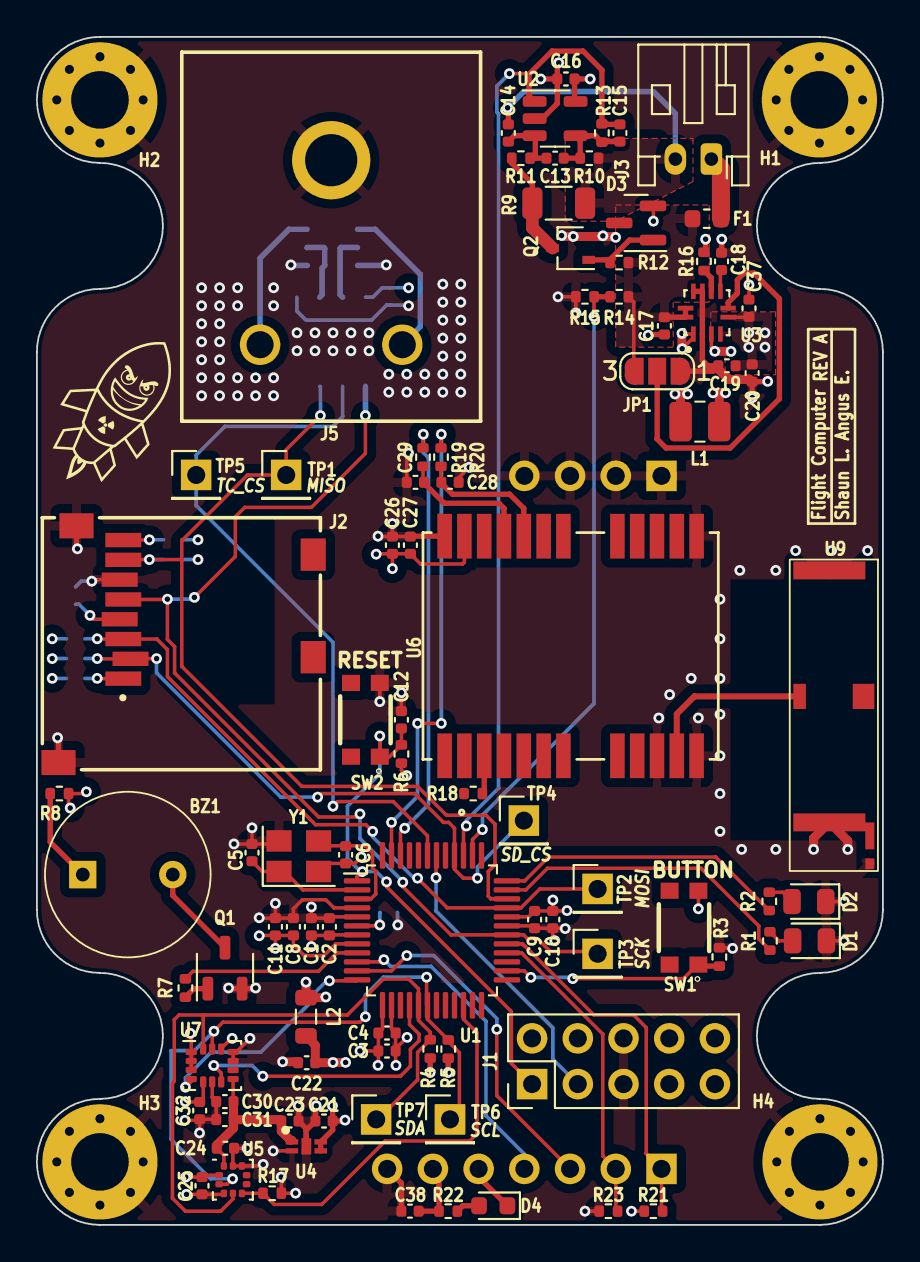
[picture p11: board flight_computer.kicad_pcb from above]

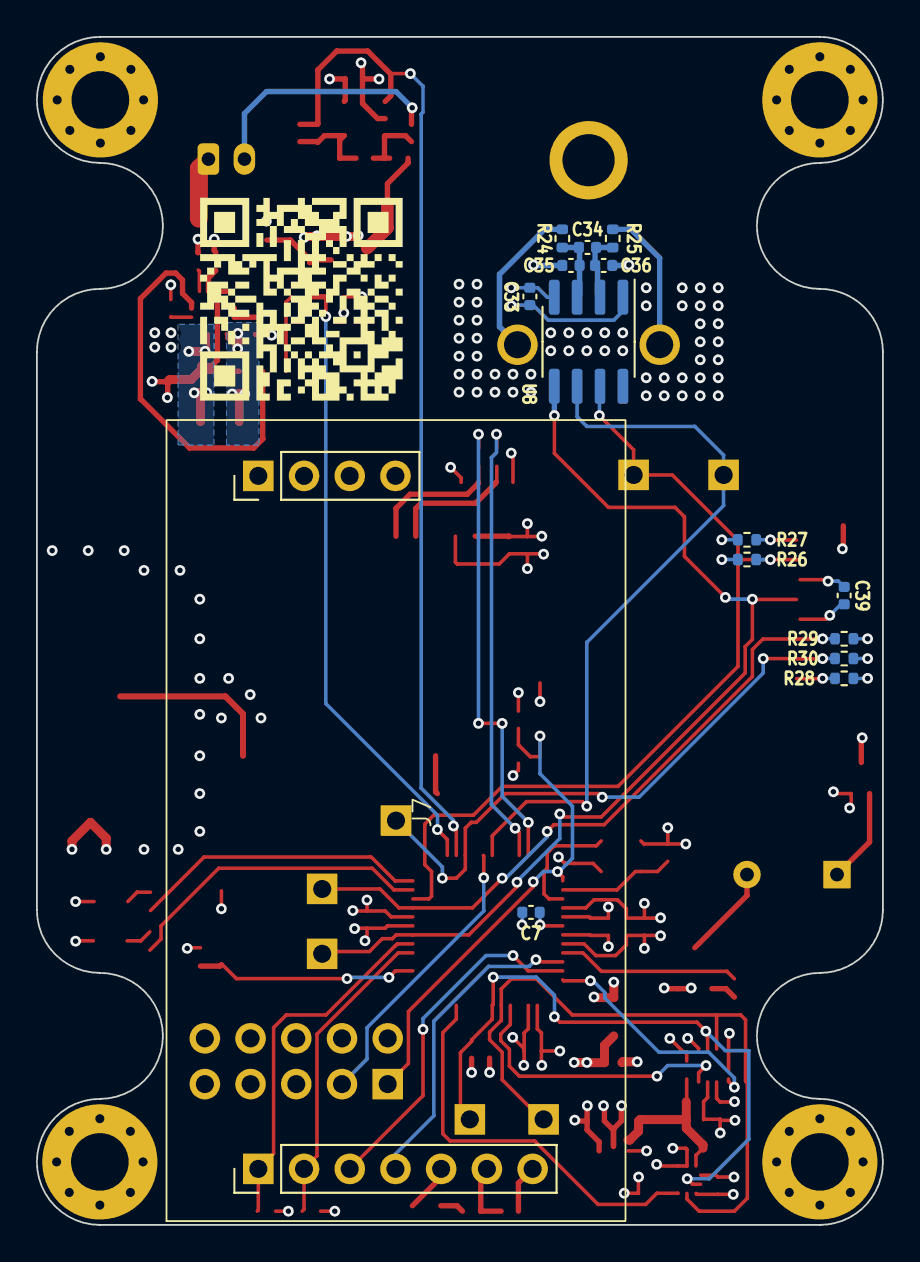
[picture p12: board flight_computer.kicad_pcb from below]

Board: 4 copper layers, 47.0 x 66.0 mm, 108 parts (15 on the bottom side), 60 nets.

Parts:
BZ1: Buzzer_indicator; buzzer_Dia9.2mm_P5mm
C1, C3, C10, C11, C17, C19, C20, C22: 10uF; C_0402_1005Metric
C2, C4, C8, C9, C12, C16, C18, C24, C25, C30, C33, C35, C36, C37, C38, C39: 100nF; C_0402_1005Metric
C5, C6: 33pF; C_0402_1005Metric
C7, C21, C23, C34: 1uF; C_0402_1005Metric
C13, C14: 1.8nF; C_0402_1005Metric
C15: 22pF; C_0402_1005Metric
C26, C31: 2.2uF; C_0402_1005Metric
C27, C32: 10nF; C_0402_1005Metric
C28, C29: 100pF; C_0402_1005Metric
D1: Green; LED_0805_2012Metric
D2: Red; LED_0805_2012Metric
D3: 5.1V; SOT-23
D4: Blue; LED_0603_1608Metric
F1: 250mA; Fuse_0603_1608Metric
H1, H2, H3, H4: MountingHole_Pad; MountingHole_3.2mm_M3_Pad_Via
J1: Conn_02x05_Odd_Even; PinHeader_2x05_P2.54mm_Vertical
J2: MEM2061-01-188-00-A_REVA; MEM2061-01-188-00-A
J3: Conn_01x02; JST_PH_S2B-PH-K_1x02_P2.00mm_Horizontal
J5: 3817564
J7: Conn_01x07_MountingPin; E220-400T30D
JP1: PFM; SolderJumper-3_P1.3mm_Open_RoundedPad1.0x1.5mm_NumberLabels
L1: 1.5uH; L_1008_2520Metric
L2: 3.3uH; L_0805_2012Metric
Q1: Q_NPN_BEC; SOT-23-3
Q2: Q_NMOS_GSD; SOT-323_SC-70
R1, R18, R22, R24, R25: 150R; R_0402_1005Metric
R2: 470R; R_0402_1005Metric
R3, R6, R14, R15, R16, R21, R23: 1M; R_0402_1005Metric
R4, R5: 4.7k; R_0402_1005Metric
R7, R10, R11: 1k; R_0402_1005Metric
R8, R19, R20: 0R; R_0402_1005Metric
R9: 0.1R; R_1206_3216Metric
R12, R26, R27, R28, R29, R30: 10k; R_0402_1005Metric
R13: 68k; R_0402_1005Metric
R17: DNP; R_0402_1005Metric
SW1, SW2: SW_Push; KMR2_1
TP1, TP2, TP3, TP4, TP5, TP6, TP7: TestPoint; PinHeader_1x01_P2.54mm_Vertical
U1: STM8S007C8T6TR; LQFP-48_7x7mm_P0.5mm
U2: NCS325; SOT-23-5
U3: TPS63051RMWR; VQFN-12-HR_2.5x2.5mm_P0.5mm
U4: MIC94310-GYMT-TR; TDFN-4-1EP_1.2x1.6mm_P0.5mm
U5: SPL07-003; ST_HLGA-10_2x2mm_P0.5mm_LayoutBorder3x2y
U6: YIC31612EBGG; 24-SMD Module
U7: ICM-42670-P; LGA-14_3x2.5mm_P0.5mm_LayoutBorder3x4y
U8: MAX31855KASA; SOIC-8_3.9x4.9mm_P1.27mm
U9: Antenna_GPS; 1582AT54A0045
Y1: 12MHz; Crystal_SMD_3225-4Pin_3.2x2.5mm

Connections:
/1V8A: C23.1, C24.1, C30.1, C31.1, U4.1 (VOUT), U5.10 (VDDA), U7.8 (VDD)
/GPS_RXD: R19.2, U1.46 (PD5)
/GPS_TXD: R20.2, U1.47 (PD6)
/IMU_FSYNC: U1.16 (PB6), U7.7 (FSYNC)
/IMU_INT: U1.12 (PA6), U7.4 (INT1/INT)
/Microcontroller/3V3D: C1.1, C2.1, C8.1, C9.1, C10.1, C11.1, C19.1, C20.1, C25.1, C26.1, C27.1, C32.1, C33.1, C37.1, C38.1, C39.1, J1.7, J1.8, J2.4 (VDD), J7.6, L2.1, R4.1, R5.1, R6.1, R8.1, R16.1, R22.2, R26.2, R27.2, R28.2, R29.2, R30.2, SW1.2, U1.7 (VDD), U1.8 (VDDIO_1), U1.32 (VDDIO_2), U3.4 (VOUT), U3.5 (FB), U5.1 (VDDIO), U6.23 (VCC), U7.5 (VDDIO), U7.12 (AP_CS), U8.4 (V_CC)
/Microcontroller/BUTTON: R3.1, SW1.1, U1.26 (PC1)
/Microcontroller/BUZZER_INDICATOR: R7.1, U1.9 (PA3)
/Microcontroller/I_{SENSE}: C15.1, R13.2, U1.39 (PE1), U2.1
/Microcontroller/LED_GREEN: R1.1, U1.35 (PG0)
/Microcontroller/LED_RED: R2.1, U1.36 (PG1)
/Microcontroller/NRST: C12.1, J1.1, R6.2, SW2.1, U1.1 (NRST)
/Microcontroller/SPI_MOSI: J2.3 (CMD), R30.1, TP2.1, U1.33 (PC6)
/Microcontroller/SPI_NSS: J2.2 (CD/DAT3), R29.1, TP4.1, U1.40 (PE0)
/Microcontroller/SWIM: J1.3, U1.42 (PD1)
/Microcontroller/VBATT_{SENSE}: R14.2, R15.1, U1.38 (PE2)
/PRESSURE_INT: R17.1, U1.22 (PB0), U5.5 (SDO)
/Power/3V3A: C3.1, C4.1, C16.1, C21.1, C22.1, L2.2, U1.13 (VDDA), U2.5 (V+), U4.3 (EN), U4.4 (VIN)
/Power/BAT_GND: C14.2, J3.2, R9.1, R10.1
/Power/I_{sense_raw}: Q2.3 (D), R9.2, R11.1
/Power/PGOOD: R16.2, U3.8 (PG)
/RADIO_M0: J7.1, R21.2, U1.29 (PC4)
/RADIO_M1: J7.2, R23.2, U1.28 (PC3)
/RADIO_RXD: J7.3, U1.11 (PA5)
/RADIO_TXD: J7.4, U1.10 (PA4)
/Radio/AUX: D4.1 (K), J7.5
/SCL: R5.2, TP6.1, U1.18 (PB4), U5.2 (SCL), U7.13 (AP_SCL/AP_SCLK)
/SDA: R4.2, TP7.1, U1.17 (PB5), U5.4 (SDA), U7.14 (AP_SDA/AP_SDIO/AP_SDI)
/SPI_MISO: J2.7 (DAT0), R26.1, TP1.1, U1.34 (PC7), U8.7 (SO)
/SPI_SCK: J2.5 (CLK), TP3.1, U1.30 (PC5), U8.5 (SCK)
/TC_CS: TP5.1, U1.43 (PD2), U8.6 (~CS)
/Temperature sensor/T+: J5.1, R24.1
/Temperature sensor/T-: J5.2, R25.1
GND: C1.2, C2.2, C3.2, C4.2, C5.1, C6.2, C7.2, C8.2, C9.2, C10.2, C11.2, C12.2, C16.2, C17.2, C18.2, C19.2, C20.2, C21.2, C22.2, C23.2, C24.2, C25.2, C26.2, C27.2, C28.2, C29.2, C30.2, C31.2, C32.2, C33.2, C35.1, C36.2, C37.2, C38.2, C39.2, D1.1 (K), D2.1 (K), D3.2 (A), H1.1, H2.1, H3.1, H4.1, J1.5, J1.6, J2.6 (VSS), J2.11 (GND), J2.12 (GND__1), J5.MH1, J7.7, J7.MP (MountPin), JP1.1 (A), Q1.2 (E), Q2.2 (S), R3.2, R15.2, R17.2, R21.1, R23.1, SW2.2, U1.4 (VSSIO_1), U1.5 (VSS), U1.14 (VSSA), U1.31 (VSSIO_2), U2.2 (V-), U3.2 (GND), U3.9 (GND), U3.10 (ILIM0), U4.2 (GND), U4.5 (EP), U5.3 (GND), U5.8 (GND), U5.9 (GND), U6.10 (GND), U6.12 (GND), U6.13 (GND), U6.24 (GND), U7.1 (AP_SDO/AP_AD0), U7.2 (RESV), U7.3 (RESV), U7.6 (GND), U7.10 (RESV), U7.11 (RESV), U8.1 (GND), U9.2 (GND), U9.4 (GND), U9.5 (CAP), Y1.2, Y1.4
unnamed: BZ1.2 (+), Q1.3 (C)
unnamed: BZ1.1 (-), R8.2
unnamed: D1.2 (A), R1.2
unnamed: D2.2 (A), R2.2
unnamed: D3.1 (K), Q2.1 (G), R12.2
unnamed: D4.2 (A), R22.1
unnamed: J2.8 (DAT1), R27.1
unnamed: J2.1 (DAT2), R28.1
unnamed: F1.1, J3.1
unnamed: C17.1, F1.2, JP1.3 (B), R12.1, R14.1, U3.11 (EN), U3.12 (VIN)
unnamed: JP1.2 (C), U3.6 (PFM/PWM)
unnamed: Q1.1 (B), R7.2
unnamed: C5.2, U1.2 (PA1/OSCIN), Y1.1
unnamed: C6.1, U1.3 (PA2/OSCOUT), Y1.3
unnamed: C7.1, U1.6 (VCAP)
unnamed: C13.2, C14.1, R11.2, U2.3 (+)
unnamed: C13.1, C15.2, R10.2, R13.1, U2.4 (-)
unnamed: L1.2, U3.1 (L1)
unnamed: L1.1, U3.3 (L2)
unnamed: C18.1, U3.7 (SS)
unnamed: R18.2, U6.3 (PPS)
unnamed: U6.11 (RF_IN), U9.1 (Feed)
unnamed: C29.1, R19.1, U6.21 (RXD)
unnamed: C28.1, R20.1, U6.20 (TXD)
unnamed: C34.1, C35.2, R24.2, U8.3 (T+)
unnamed: C34.2, C36.1, R25.2, U8.2 (T-)

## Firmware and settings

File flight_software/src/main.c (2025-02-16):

#include "common.h"
#include "gpio.h"
#include "ebyte_radio.h"
#include "SPL07_pressure.h"
#include "YIC_gps.h"
#include "i2c_driver_STM8S007.h"
#include "ICM42670_imu.h"
#include "inttypes.h"
#include "MAX31855_therm.h"
#include "battery.h"

void assert_failed(uint8_t* file, uint32_t line);
static void clock_config(void);
void init_watchdog(void);

#define MAIN_LOOP_FREQ_HZ 20 // 20 mins logging 200 chars @ 50 Hz is around 12 mB.

void main(void)
{
  clock_config();
  GPIO_Init(GREEN_LED_PORT, GREEN_LED_PIN, GPIO_MODE_OUT_PP_LOW_FAST);
  GPIO_Init(RED_LED_PORT, RED_LED_PIN, GPIO_MODE_OUT_PP_LOW_FAST);
  GPIO_Init(M0_RADIO_PORT, M0_RADIO_PIN, GPIO_MODE_OUT_PP_LOW_FAST);
  GPIO_Init(M1_RADIO_PORT, M1_RADIO_PIN, GPIO_MODE_OUT_PP_LOW_FAST);
  radio_uart_init();

  radio_print_debug("Radio initialized\r\n");

  init_battery_measurements();
  i2c_init();
  imu_init(); // Needs i2c_init called first
  spl07_init(); // Needs i2c_init called first
  gps_init();
  thermo_init();
  
  uint32_t loop_start_time;
  uint32_t current_time;
  
  //init_watchdog();
  while (1){
    IWDG_ReloadCounter(); // Reload watchdog
    loop_start_time = millis();
    GPIO_WriteReverse(GREEN_LED_PORT, GREEN_LED_PIN);

    // Read all sensors
    read_gps_buffer();
    update_imu_state();
    spl07_update_baro();
    read_batt_voltage();
    read_batt_current();
    update_thermo_state();

    // Log to SD
    send_telemetry();
    
    // Paced loop, wait until time to continue
    current_time = millis();
    while(current_time - loop_start_time < (1000 / MAIN_LOOP_FREQ_HZ))
    {
      current_time = millis();
    }
  }
}

void init_watchdog(void)
{
  // Desire 0.5s watchdog timeout
  // T = 2*T_LSI * P * R
  // T_LSI = 128 kHz
  // Choose P = 256, R = 125 gives T = 0.5s
  IWDG_Enable();
  IWDG_WriteAccessCmd(IWDG_WriteAccess_Enable);
  IWDG_SetPrescaler(IWDG_Prescaler_256);
  IWDG_SetReload(0xFE);
  IWDG_ReloadCounter();
  //IWDG_WriteAccessCmd(IWDG_WriteAccess_Disable);  
}

void clock_config(void)
{
  CLK_HSIPrescalerConfig(CLK_PRESCALER_HSIDIV1);
  CLK_SYSCLKConfig(CLK_PRESCALER_CPUDIV1);
  TIM4_Config();
}

void print_bits_of_byte(uint8_t byte)
{
  char bits[9];
  for (int i = 0; i < 8; i++)
  {
    bits[i] = (byte & (1 << (7-i))) ? '1' : '0';
  }
  bits[8] = '\0';
  radio_print_debug(bits);
}

int32_t getTwosComplement(uint32_t raw, uint8_t length) {
  uint32_t comparison = (uint32_t)1<<(length - 1);
  int32_t result = 0;

  // Check if the sign bit is set
  if (raw & comparison) {
      // If the sign bit is set, convert to two's complement
      uint32_t mask = ((uint32_t)1 << length) - 1; // inverting mask
      raw = (raw ^ mask) + 1; // Invert each bit then add one
      result = -1 * (int32_t)raw; // Make it negative
  } else {
      // If the sign bit is not set, it's already a positive value
      result = (int32_t)raw;
  }
  return result;
}


#ifdef USE_FULL_ASSERT

/**
  * @brief  Reports the name of the source file and the source line number
  *   where the assert_param error has occurred.
  * @param file: pointer to the source file name
  * @param line: assert_param error line source number
  * @retval None
  */
void assert_failed(uint8_t* file, uint32_t line)
{ 
  /* User can add his own implementation to report the file name and line number,
     ex: printf("Wrong parameters value: file %s on line %d\r\n", file, line) */
  /* Infinite loop */
  while (1)
  {
    char buff[1000];
    #ifdef DEBUG_ENABLE
    sprintf(buff, "Wrong parameters value: file %s on line %d\r\n", file, line);
    radio_print_debug(buff);
    #endif
    GPIO_WriteReverse(GREEN_LED_PORT, GREEN_LED_PIN);
    delay_ms(2000);
  }
}
#endif

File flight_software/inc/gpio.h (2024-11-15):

#pragma once

#include "common.h"

#define GREEN_LED_PORT  GPIOG
#define GREEN_LED_PIN   GPIO_PIN_0 // This is pin PG0, or pin 35 on the schematic.

#define RED_LED_PORT  GPIOG
#define RED_LED_PIN   GPIO_PIN_1 // This is pin PG1, or pin 36 on the schematic.

#define M0_RADIO_PORT GPIOC
#define M0_RADIO_PIN GPIO_PIN_4

#define M1_RADIO_PORT GPIOC
#define M1_RADIO_PIN  GPIO_PIN_3

#define THERMO_CHIP_PORT GPIOD
#define THERMO_CHIP_PIN_SELECT  GPIO_PIN_2 // This is pin PD2, or pin 43 on the schematic.

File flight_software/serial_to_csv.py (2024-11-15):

import serial
import threading
import csv
from collections import deque
import time
import msvcrt  # For capturing keyboard input on Windows

# Configuration for serial port and circular buffer
SERIAL_PORT = 'COM6'
BAUDRATE = 115200
BUFFER_SIZE = 10  # Size of circular buffer

# Circular buffer (deque)
circ_buffer = deque(maxlen=BUFFER_SIZE)

# Condition variable to synchronize threads
buffer_not_empty = threading.Condition()

# Flag to signal threads to stop
stop_threads = threading.Event()

# Thread function to read lines from serial port
def read_serial():
    ser = serial.Serial(SERIAL_PORT, baudrate=BAUDRATE, timeout=1)
    print(f"Listening on {SERIAL_PORT}...")
    try:
        while not stop_threads.is_set():
            if ser.in_waiting > 0:
                line = ser.readline().decode('utf-8').strip()  # Read a line from the serial port
                if line:
                    with buffer_not_empty:
                        circ_buffer.append(line)  # Add the line to the circular buffer
                        print(f"Added to buffer: {line}")
                        buffer_not_empty.notify()  # Notify the other thread that the buffer is not empty
    except Exception as e:
        print(f"Error: {e}")
    finally:
        ser.close()

# Thread function to write lines to CSV
def write_to_csv():
    with open('output.csv', mode='a', newline='') as csvfile:
        csv_writer = csv.writer(csvfile)
        while not stop_threads.is_set():
            with buffer_not_empty:
                while len(circ_buffer) == 0:
                    buffer_not_empty.wait()  # Wait until the buffer is not empty
                    if stop_threads.is_set():  # Exit if stop signal is set
                        break
                if len(circ_buffer) > 0:
                    line = circ_buffer.popleft()  # Get the line from the buffer
                    print(f"Writing to CSV: {line}")
                    csv_writer.writerow([line])  # Write the line to the CSV

# Function to detect Esc key press
def wait_for_esc():
    print("Press 'Esc' to stop...")
    while True:
        if msvcrt.kbhit():
            if ord(msvcrt.getch()) == 27:  # 27 is the ASCII code for Esc
                print("Esc pressed, stopping...")
                stop_threads.set()  # Signal threads to stop
                break
        time.sleep(0.1)

# Main function to start threads
def main():
    # Create and start the serial reader and CSV writer threads
    reader_thread = threading.Thread(target=read_serial)
    writer_thread = threading.Thread(target=write_to_csv)
    esc_thread = threading.Thread(target=wait_for_esc)

    reader_thread.start()
    writer_thread.start()
    esc_thread.start()

    reader_thread.join()
    writer_thread.join()
    esc_thread.join()

if __name__ == "__main__":
    main()

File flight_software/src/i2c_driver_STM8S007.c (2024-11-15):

#include "common.h"
#include "i2c_driver_STM8S007.h"

void i2c_init(void)
{
    I2C_Cmd(ENABLE);
    I2C_Init(80000, 0x69, I2C_DUTYCYCLE_2, I2C_ACK_CURR, I2C_ADDMODE_7BIT, F_CPU/1000000);
}

uint8_t i2c_write_and_verify_byte(uint8_t device_address, uint8_t register_address, uint8_t byte, uint8_t write_mask)
{
    i2c_write_byte(device_address, register_address, byte);
    uint8_t ret_val[1];
    i2c_read(device_address, register_address, ret_val, 1);
    // char buff[100];
    // sprintf(buff, "Register 0x%x has value = ", register_address);
    // radio_print_debug(buff);
    // print_bits_of_byte(ret_val[0]);
    // radio_print_debug("\r\n");

    for (int i=0; i<8; i++)
    {   
        if ((write_mask >> i) & 1) // Need to check the bit
        {
            uint8_t bit_mask = 1<<i;
            if ((ret_val[0] & bit_mask) != (byte & bit_mask))
            {
                return I2C_FAILURE;
            }
        }
    }

    return I2C_SUCCESS;

}

void i2c_read(uint8_t device_address, uint8_t register_address, uint8_t bytes[], uint8_t num_bytes)
{
    if (num_bytes > 1) I2C_AcknowledgeConfig(I2C_ACK_CURR); // Need to ack the bytes recieved so that we keep reading;
    else I2C_AcknowledgeConfig(I2C_ACK_NONE); // Send a nack on next byte recieved

    // TODO: add timeouts to whiles
    I2C_GenerateSTART(ENABLE);
    while(!I2C_CheckEvent(I2C_EVENT_MASTER_MODE_SELECT)) continue;

    //radio_print_debug("Addr W\r\n");
    I2C_Send7bitAddress(device_address, I2C_DIRECTION_TX);
    while(!I2C_CheckEvent(I2C_EVENT_MASTER_TRANSMITTER_MODE_SELECTED)) continue;

    //radio_print_debug("Data\r\n");
    I2C_SendData(register_address);
    while(!I2C_CheckEvent(I2C_EVENT_MASTER_BYTE_TRANSMITTED)) continue;
    
    //radio_print_debug("Repeated start\r\n");
    I2C_GenerateSTART(ENABLE);
    while(!I2C_CheckEvent(I2C_EVENT_MASTER_MODE_SELECT)) continue;

    //radio_print_debug("Addr R\r\n");
    I2C_Send7bitAddress(device_address, I2C_DIRECTION_RX);
    while(!I2C_CheckEvent(I2C_EVENT_MASTER_RECEIVER_MODE_SELECTED)) continue;

    // Read bytes with ack (if reading multiple bytes)
    for (int i=0; i<num_bytes - 1; i++) // -1 as we must NACK the last byte
    {
        while(!I2C_CheckEvent(I2C_EVENT_MASTER_BYTE_RECEIVED)) continue;
        bytes[i] = I2C_ReceiveData();
    }

    // Nack to next byte recieved
    I2C_AcknowledgeConfig(I2C_ACK_NONE); // Send a nack on next byte recieved to let slaveknow we are done
    while(!I2C_CheckEvent(I2C_EVENT_MASTER_BYTE_RECEIVED)) continue;
    bytes[num_bytes-1] = I2C_ReceiveData();
    
    I2C_GenerateSTOP(ENABLE);
}

void i2c_write_byte(uint8_t device_address, uint8_t register_address, uint8_t byte)
{
    // TODO: add timeouts to whiles
    // radio_print_debug("Start\r\n");
    I2C_GenerateSTART(ENABLE);
    while(!I2C_CheckEvent(I2C_EVENT_MASTER_MODE_SELECT)) continue;

    // radio_print_debug("Chip addr\r\n");
    I2C_Send7bitAddress(device_address, I2C_DIRECTION_TX);
    while(!I2C_CheckEvent(I2C_EVENT_MASTER_TRANSMITTER_MODE_SELECTED)) continue;

    // radio_print_debug("Reg addr\r\n");
    I2C_SendData(register_address);
    while(!I2C_CheckEvent(I2C_EVENT_MASTER_BYTE_TRANSMITTED)) continue;

    // radio_print_debug("Data\r\n");
    I2C_SendData(byte);
    while(!I2C_CheckEvent(I2C_EVENT_MASTER_BYTE_TRANSMITTED)) continue;

    // radio_print_debug("Stop\r\n");
    I2C_GenerateSTOP(ENABLE);
}

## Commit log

2024-04-25 Start of flight computer PCB
    [flight_computer.kicad_pcb, flight_computer.kicad_sch]
2024-04-26 Finished power input design
    [MCU.kicad_sch, flight_computer.kicad_sch, power.kicad_sch]
2024-04-28 MCU circuit started
    [MCU.kicad_sch]
2024-04-28 Adding current shunt measurement, amplification, filtering
    [power.kicad_sch]
2024-04-29 Buzzer, LEDs, added actual components for current sensing and others I had missed
    [MCU.kicad_sch, flight_computer.kicad_sch, power.kicad_sch]
2024-04-29 SD card
    [MCU.kicad_sch]
2024-04-30 PRessure sensor circuit
    [MCU.kicad_sch, flight_computer.kicad_sch, power.kicad_sch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]
2024-05-06 Tidying up schematics and adding most missing sections (Not finished GPS)
    [MCU.kicad_sch, flight_computer.kicad_sch, gps.kicad_sch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]
2024-05-08 Finishing gps, ready to connect all
    [MCU.kicad_sch, flight_computer.kicad_sch, gps.kicad_sch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]
2024-05-08 Schematic connecting
    [MCU.kicad_sch, flight_computer.kicad_sch, imu.kicad_sch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]
2024-05-10 ERC complete
    [MCU.kicad_sch, gps.kicad_sch, imu.kicad_sch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]
2024-05-10 Part way through review
    [MCU.kicad_sch, flight_computer.kicad_sch, gps.kicad_sch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]
2024-05-10 Adding shauns thermcoouple
    [MCU.kicad_sch, gps.kicad_sch, imu.kicad_sch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]
2024-05-11 Thermocouple circuit done
    [MCU.kicad_sch, flight_computer.kicad_sch, temp_sensor.kicad_sch]
2024-05-11 Clean PCb del
    [flight_computer.kicad_pcb]
2024-05-11 Start of PCB
    [flight_computer.kicad_pcb]
2024-05-12 testing kicad version compatibility
    [flight_computer.kicad_pcb]
2024-05-12 KiCAD8 is not compatible with 7: Revert "testing kicad version compatibility"
    This reverts commit 37378f71d3b59c33c1abc1999dff2b71273f3631.
    [flight_computer.kicad_pcb]
2024-05-16 A hearty attempt at CPU wiring.
    [flight_computer.kicad_pcb]
2024-05-16 Start of layout
    [MCU.kicad_sch, flight_computer.kicad_pcb, imu.kicad_sch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]
2024-05-18 finsihed grouping the layout
    [flight_computer.kicad_pcb, power.kicad_sch, radio.kicad_sch]
2024-05-19 Layout first effort done
    [Flight computer outline.dxf, MCU.kicad_sch, flight_computer.kicad_pcb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]
2024-05-19 GPS antenna controlled impedance
    [flight_computer.kicad_pcb, gps.kicad_sch]
2024-05-20 More PCB layout
    [MCU.kicad_sch, flight_computer.kicad_pcb]
2024-05-24 Adding E220-400T30D footprint and 3D model
    [flight_computer.kicad_pcb, radio.kicad_sch]
2024-05-24 a routing attempt
    [flight_computer.kicad_pcb]
2024-05-26 Most of the way through relayout and new antenna
    [Flight computer outline.dxf, MCU.kicad_sch, flight_computer.kicad_pcb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]
2024-05-26 Antenna routing, and other routing done
    [flight_computer.kicad_pcb, gps.kicad_sch]
2024-05-28 Moving antenna and removing matching circuit
    [flight_computer.kicad_pcb, gps.kicad_sch]
2024-05-28 First draft of PCB routing complete
    [MCU.kicad_sch, flight_computer.kicad_pcb]
2024-05-28 DRC gone, not reviews yet
    [flight_computer.kicad_pcb]
2024-05-28 Most warnings gone now too
    [flight_computer.kicad_pcb]
2024-05-28 ERC okay
    [gps.kicad_sch]
2024-05-29 PCB review done
    [flight_computer.kicad_pcb]
2024-05-29 revA sent for production
    [flight_computer-B_Cu.gbl, flight_computer-B_Mask.gbs, flight_computer-B_Paste.gbp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]
2024-07-20 Adding SDCC user manual annotated and some makefile notes
    [flight_computer.csv, flight_computer.kicad_sch, gps.kicad_sch]
2024-07-29 uart radio working
2024-08-06 I2C doesnt work
2024-08-09 I2C progress, not working yet
    [SPL07_pressure.c, ebyte_radio.c, main.c]
2024-08-10 Working I2C read function
2024-08-12 Fixing makefile + i2c write
    [SPL07_pressure.c]
2024-08-12 write and verify i2c byte function
2024-08-12 reading something pressure, not quite there tho
2024-08-21 Temp calc working, pressure not
2024-08-24 almost fixed 2s compliment
    [SPL07_pressure.c, main.c, tempCodeRunnerFile.py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]
2024-08-24 spl07 pressure and temp readings complete, separate I2C module
2024-08-25 no ack from imu
2024-08-28 working IMU init
2024-08-28 Imu working
2024-08-29 start of interrupts
2024-08-29 Uart ISR at least being called
2024-08-31 sorta working minmea, something wrong with my circ buffer, two messages are trying to be decoded as 1
    [YIC_gps.c]
2024-09-02 SPI working, SD card not fully initing
2024-09-10 working imu fosho
2024-09-12 just sending floats over radio is goal
    [output.csv]
2024-09-16 sample radio output
2024-10-08 start of esp32
    [MCU.kicad_sch]
2024-10-11 RevB PCB work
    [MCU.kicad_sch, flight_computer.kicad_sch]
2024-10-12 adc voltage reading
2024-10-12 battery voltage calibrated
2024-10-18 Both battery voltage and current readings calibrated
2024-10-18 Example log
    [LOG.csv]
2024-10-23 Fixed freezing issue #14
    [YIC_gps.c, main.c]
2024-11-04 Pretty sure code is right, need to check board.
2024-11-06 Full code done but freezing issue is back
    [MAX31855_therm.c, ebyte_radio.c, main.c]
2024-11-10 made some progress on heat conduction, stopping here for now
2024-11-10 Got basic setup working, need to figure out how to add in stl
    [Nose cone.step]
2024-11-13 Watchdog implemented, and does work but sometimes the reboot gets stuck during GPS init and thus it dies anyway. Initial frezing issue not solved with delay in the circ buff read
    [YIC_gps.c, ebyte_radio.c, main.c]
2025-02-15 log to csv
    [LOG00037.csv]
2025-08-31 Dead reckoning basic
    [flight_data_trimmed.csv, reconstruction_out.csv]
2025-09-06 Animation working
    [reconstruction_out.csv]
2025-09-06 trajectory gif
    [reconstruction_out.csv]
2025-09-06 Added basic complementary filter
    [reconstruction_out.csv]
2025-09-06 Tuned to match video
    [reconstruction_out.csv]
2025-09-06 better timed gif
    [flight_data_trimmed.csv, reconstruction_out.csv]
